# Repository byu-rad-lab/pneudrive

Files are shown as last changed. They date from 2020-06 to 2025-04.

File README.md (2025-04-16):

# PneuDrive Pressure Control System

This repository contains all of the designs, code, and instructions needed to create a low level pressure controller designed for pneumatically actuated robots. This pressure controller is designed to use relatively inexpensive off-the-shelf components and to favor simplicity in an effort to make it easy to understand and adapt for different applications.

Here is a [video](https://bit.ly/3QkrEqO) that is a brief overview of the system.

<!-- add picture of boards from resources folder -->
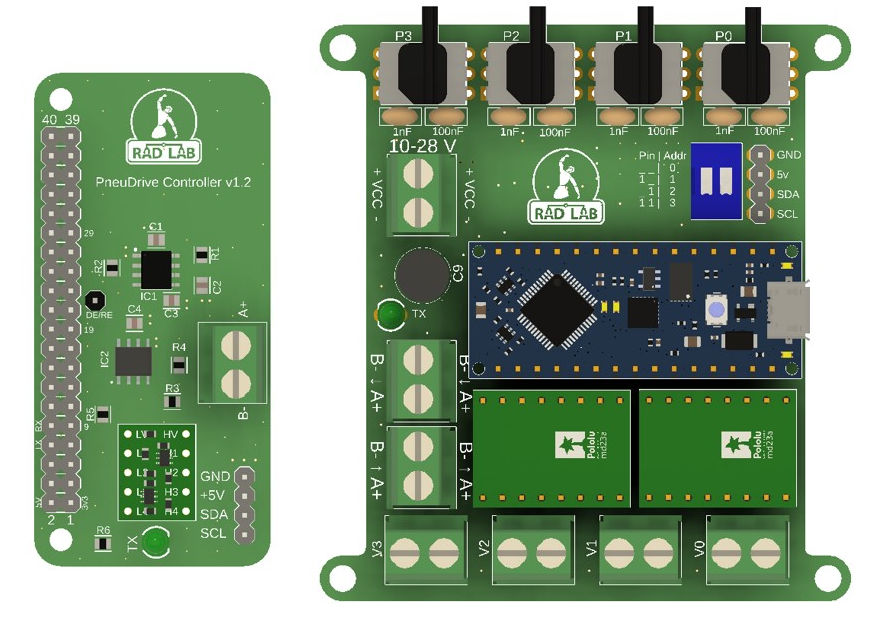
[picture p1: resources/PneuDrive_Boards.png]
PneuDrive boards


The pressure control system consists of one single-board-computer (SBC) acting as the ROS master and communicating serially with one or more Arduinos. The SBC needs to be capable of running ROS/Ubuntu (e.g. Raspberry Pi, NVIDIA Jetson, Odroid). We use the [ODROID N2+](https://www.hardkernel.com/shop/odroid-n2-with-4gbyte-ram-2/). We also provide python bindings that allow you to interact with the pressure controller without ROS.

Each Arduino performs high-rate (~1 kHz) pressure control of up to 4 chambers and transmits pressure data back to the ROS master. A high level diagram of the pressure control system can be seen in the figure below:

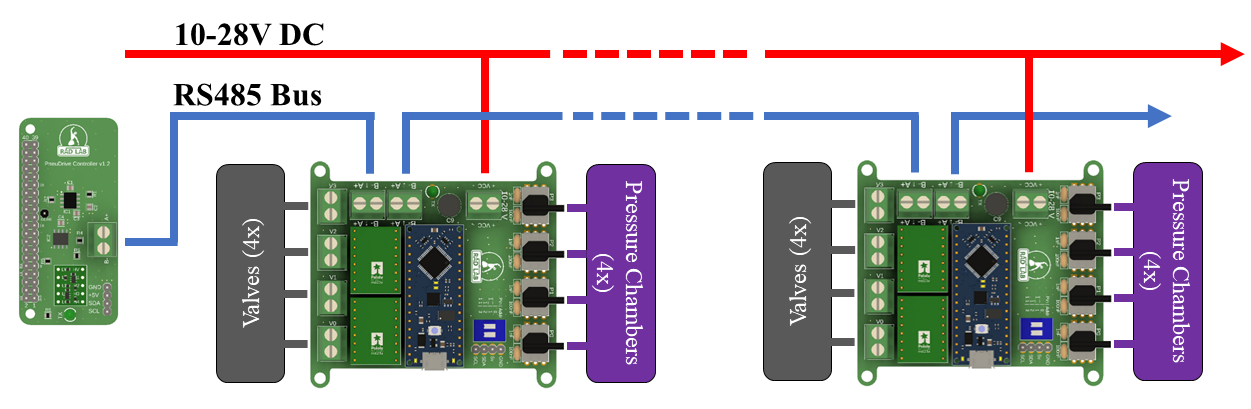
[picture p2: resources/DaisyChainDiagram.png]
PneuDrive system


## Dependencies

## Installation
If the SBC is connected to the internet, the easiest way to use PneuDrive is to clone the repository directly onto the SBC. If the SBC is not connected to the internet, you can clone the repository onto another computer and then copy it over to the SBC using a tool like scp over a local network:

``` console
scp -r <path to pneudrive on computer> <username@SBC_IP_ADDRESS>:<path to desired location on SBC>
```

If you intend to use PneuDrive with ROS, just make sure the package is placed into the src directory of a ROS workspace. Once the pneudrive package in in the src directory, you can build it using ```colcon build``` from the root of the workspace.

If you intend to use PneuDrive without ROS (i.e. using the python bindings), you can place the package anywhere on the SBC. Python bindings are implemented using pybind11, so when cloning the repository, it is important to pass ```--recurse-submodules``` to git to ensure that pybind11 is cloned as well:

``` console
git clone --recurse-submodules <git url>
```

To build the bindings, you will just need to navigate to the python_bindings directory and build the bindings manually with cmake:

``` console
cd python_bindings
mkdir build
cd build
cmake ..
make
```

## How is it organized

This repository is structured as a ROS package. It is designed to be placed in a ROS workspace on the SBC used for pressure control. There are however several other directories not necessary for a ROS package:

* **pcb_design** - this directory contains all of the wiring diagrams and PCB schematics. Instructions for the population of the PCB as well as wiring the entire pressure controller are found here.
* **odroid_setup** - this directory contains all of instructions and files necessary to set up an ODROID for use as the ROS master in a pressure control system.
* **arduino_firmware** - this directory contains the instructions and code needed to program the arduinos to act as high rate pressure controllers.
* **python_bindings** - this directory contains python bindings to interact with PneuDrive independent of ROS, in a python scripting environment.

## Steps to create a pressure control system

1. Use the instructions and schematics in the **pcb_design** directory to order and assemble the necessary components to construct a PneuDrive controller PCB and several embedded PCBs.
2. Use the instructions and files in the **odroid_setup** directory to setup the SBC as the ROS master
3. Use the instructions and files in the **arduino_firmware** directory to program each arduino as a high-rate pressure controller

## Running the PneuDrive ROS Node

Once the SBC boots up it you can ssh into it with ```ssh ubuntu@192.168.0.xxx```. The username is ```ubuntu``` and the password is ```temppwd```. This process might be slightly different depending on your SBC.

Once you are logged in, you can launch the pressure control ROS node (along with a roscore) using the following command:

``` shell
ros2 launch pneudrive rs485_pressure.launch.py numjoints:=[number of joints]
```

where the ```numjoints``` command line argument is required and tells the node how many joints to look for on the serial bus. 

This creates a ROS node called "PressureController". Depending on ```numjoints```, the node will create addresses for each joint. The node then creates publishers and subscribers for every joint specified by the addresses. If the SBC cannot find all of the specified addresses, the node throw an error and shut down. If this happens, here are some common fixes:

* Make sure your wires are all connected securely and correctly.
* Make sure that each pressure control board dip switch is set to the proper address. The dip switch positions are printed on the pcb and they should match what is specified in the yaml file. For example, if I have a 3 joint arm, I would make sure that the first joint is set to 0 then the next as 1 and the last as 2, with those same addresses specified in the code. 
* Make sure you didn't flip the A+ and B- wires when wiring up the connectors. We chose to use screw terminals for ease of use, but this does make flipping wires easier if you aren't being careful. 

When the node launches, it will print out all of the joints it detected and start the node.

## Citation

If you use PneuDrive in your research, please cite the our paper:

```bibtex

 @inproceedings{
	 Johnson_Cheney_Cordon_Killpack_2024, 
	 address={San Diego, CA, USA}, 
	 title={PneuDrive: An Embedded Pressure Control System and Modeling Toolkit for Large-Scale Soft Robots}, 
	 rights={https://doi.org/10.15223/policy-029}, 
	 ISBN={9798350381818}, 
	 url={https://ieeexplore.ieee.org/document/10521958/}, 
	 DOI={10.1109/RoboSoft60065.2024.10521958}, 
	 booktitle={2024 IEEE 7th International Conference on Soft Robotics (RoboSoft)}, 
	 publisher={IEEE}, 
	 author={Johnson, Curtis C. and Cheney, Daniel G. and Cordon, Dallin L. and Killpack, Marc D.}, 
	 year={2024}, 
	 month=apr, 
	 pages={786–792}, 
	 language={en} 
 }

```

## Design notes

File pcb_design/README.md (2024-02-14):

This directory contains everything you need to order and assemble the PCBs needed for PneuDrive. 

# PnueDrive Controller Board
### Design Files
1. All design files (Bill of Materials, 3d step file, .sch, .brd, and a pdf of the schematic) are located in PnueDrive-Controllerv1.2-Designs.zip.

### Ordering PCB
1. Any PCB manufacturer can be used, but we have used JLCPCB in the past. Go to their [website](https://jlcpcb.com/), click upload gerber file, and upload pneudrive_controllerv1.2_gerbers.zip. After processing, it should say "Detected 4 layer board of 65x31mm(2.56x1.22 inches) ."
2. Every manufacturing option can remain default except for the following: **Remove Order Number: Specify a Location**
3. If you want, you can order a stencil to make soldering the SMT components easier. We have not done this since there are only 1 or 2 controller boards that need to be assembled.

### Ordering Components
1. The Bill of Materials (BoM) PneuDrive BoM - Controllerv1.2.pdf. The BoM contains links to purchase components, descriptions, and part numbers. The total price as of 2023 is $5.87 USD.
2. You will also need female headers to plug things into and the logic level shifter from pololu.

### Assembly
1. Solder the SMT components to the board before any of the through hole components. This is because the through hole components will get in the way of the hot air rework station. [Here](https://www.youtube.com/watch?v=fYInlAmPnGo&pp=ygUWc210IHNvbGRlcmluZyB0dXRvcmlhbA%3D%3D) is a good tutorial on how to do SMT soldering.

# PneuDrive Embedded Board
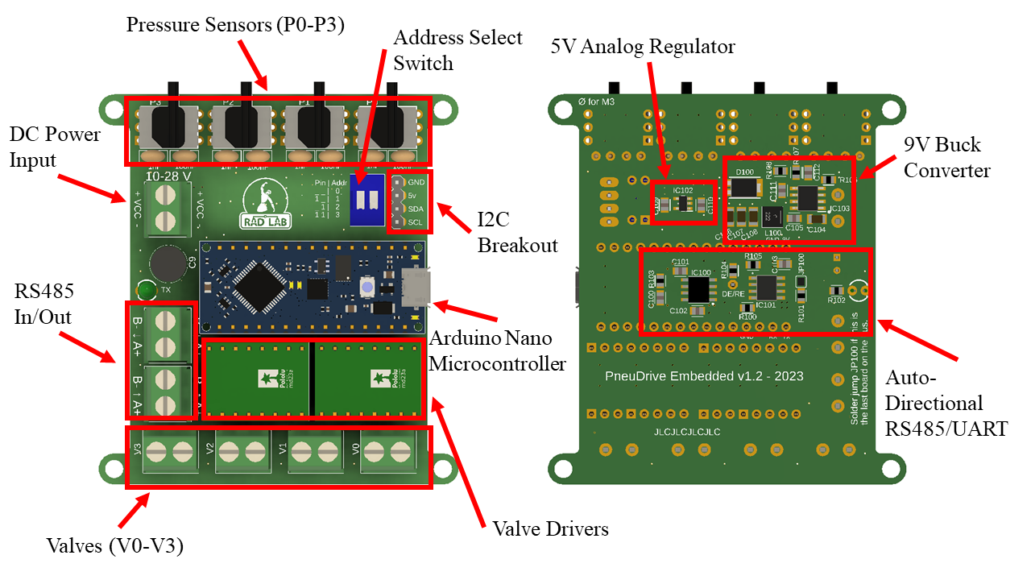
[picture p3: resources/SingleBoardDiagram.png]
Embedded Board


### Design Files
1. All design files (Bill of Materials, 3d step file, .sch, .brd, and a pdf of the schematic) are located in PneuDrive-Embeddedv1.2-Designs.zip.

### Ordering PCB
1.  Go to their [website](https://jlcpcb.com/), click upload gerber file, and upload pneudrive_embeddedv1.2_gerbers.zip After processing, it should say "Detected 4 layer board of 75x69mm(2.95x2.72 inches)."
2.  Every option can remain default except for the following: **Remove Order Number: Specify a Location**
3.  Order Stencil together with PCB. This costs extra, but since the embedded boards typically are assembled in volume, it is worth it.
4.  All the stencil options can stay default except the following: **Stencil Side: Bottom**

### Ordering Components
1. The Bill of Materials (BoM) PneuDrive BoM - Embeddedv1.2.pdf. The BoM contains links to purchase components, descriptions, and part numbers. The total price as of 2023 is $156.74 USD.
2. You will also need female headers to plug things into and the a4990 motor driver breakouts from pololu.

### Assembly
1. Solder the SMT components on the bottom before any of the through hole components. This is because the through hole components will get in the way of the hot air rework station. [Here](https://www.youtube.com/watch?v=fYInlAmPnGo&pp=ygUWc210IHNvbGRlcmluZyB0dXRvcmlhbA%3D%3D) is a good tutorial on how to do SMT soldering.

# Consumables

For assembly, we used the following:
*  [Solder Paste](https://www.amazon.com/Wonderway-Soldering-Electronics-CELLPHONE-Repairing/dp/B0BLSJQPR6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) ~$15 USD
*  [Flux](https://www.amazon.com/Smooth-Flow-No-Clean-syringe-plunger/dp/B08KJRCYRH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) ~$15 USD
*  [Solder Wire](https://www.amazon.com/Dia0-032in-0-11lb-Precision-Electronics-Soldering/dp/B07Q167J98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) ~$10 USD

# Tools
You'll need
* A soldering iron
* A hot air rework station (for SMT components)

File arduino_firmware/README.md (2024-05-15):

# PneuDrive Firmware

## Introduction
This Arduino code is designed for controlling valves using the A4990 motor driver and interfacing with pressure sensors. It provides functionality for reading pressure data and adjusting valve positions accordingly. The code and hardware is designed for each module to be a node on an RS485 bus for high speed and robust communication.

## Valve Command Signals
Valve PWM commands are on the interval [-400, 400]. 
- -400 corresponds to commanding -1 amp (vent), and 400 corresponds to +1 amp (fill).
- The driver boards actively limit current to 0.7 amps, so any command above 0.7 amps will result in 0.7 amps on the hardware.

## Timer Frequencies
- The code makes use of timers for PWM control. It changes the timer frequencies to eliminate annoying hum when controlling the valves.
- Note that changing timer frequencies may affect the built-in delay() and millis() functions.

## Dependencies
- This code relies on the `A4990ValveInterface` library.

## Installation
1. Ensure you have the necessary hardware set up (i.e. the PCBs are all built)
2. We use the [PlatformIO extension](https://marketplace.visualstudio.com/items?itemName=platformio.platformio-ide), so the configuration files are already included. If you are using the Arduino IDE, you will need to manually install the libraries and configure the project. 
3. Open this directory with Platform IO
4. Install the required Arduino libraries (if using Arduino IDE), or let PlatformIO do that for you based on the platform.ini
5. Upload main.cpp to your Arduino Nano Every from PlatformIO. 

## Usage
1. Connect the pressure sensors as specified in the code.
2. Adjust the parameters like `MAX_INPUT`, `saturation_error`, and `kp` to suit your application.
3. Monitor valve commands and pressure data through the Serial monitor if `DEBUG_MODE` is enabled.
4. Use the code to control valves and read pressure data as needed.

## Functions and Their Descriptions

### `byteToShorts(unsigned short *short_array, const byte *byte_array)`
- Converts an array of 8 bytes to an array of 4 shorts.
- Used to decode incoming data.

### `shortToBytes(const unsigned short *short_array, byte *byte_array)`
- Converts an array of 5 shorts to an array of 10 bytes in big-endian format.
- Used to prepare outgoing data.

### `handleIncomingBytes()`
- Handles incoming data from the Serial port.
- Checks for device addresses and processes pressure commands.
- Responds with pressure data if the device address matches.

### `readPressureData()`
- Reads pressure data from analog pins and stores it for use in control.

### `custom_delay(int seconds)`
- Custom delay function for waiting a specified number of seconds since we can't use the built-in delay() function with the modified timer frequencies.

### `getrs485address()`
- Retrieves the RS485 address based on the state of DIP switches.

### `speedupPWM()`
- Configures timer frequencies to eliminate audible noise from valve control.

### `setup()`
- Initializes the hardware and serial communication.
- Sets up timer frequencies and other parameters.

### `loop()`
- The main loop of the program.
- Reads pressure data, processes it, and adjusts valve commands accordingly.

## Author
- Curtis Johnson

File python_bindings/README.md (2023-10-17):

To build the bindings, you will just need to navigate to the python_bindings directory and build the bindings manually with cmake:

``` console
cd python_bindings
mkdir build
cd build
cmake ..
make
```

Once they are built, an importable python module called pneudrive_py will show up as a shared library in the build directory. You can import this module into any python script and use it to communicate with the pressure controllers. Here is a simple example:

``` python
import numpy as np
from pneudrive_py import PressureController

uart_port = '/dev/ttyS1'
num_devices = 4
my_controller = PressureController(uart_port, num_devices)

#check communication with all expected devices
my_controller.ping_devices()

pressure_cmd = np.array([1,2,3,4])
for i in range(num_devices):
    my_controller.set_pressure_commands(i, pressure_cmd)
    data = my_controller.get_pressure_data(i)

```

Setting the pressure commands for the ith device using ``` set_pressure_commands()``` initiates a call and repsonse transmission. The SBC controller will send the commands to the embedded device and the embedded device will respond with pressure measurements, accessible in Python via ``` get_pressure_data()```. 

Note that this means that successive calls to ```get_pressure_data()``` for the same device will return the same data. If you want to get new data, you will need to call ```set_pressure_commands()``` again.

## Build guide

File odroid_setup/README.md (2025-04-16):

## Setting Up an Odroid with Ubuntu for Pneumatic Drive Control

### Requirements

- [Download Balena Etcher](https://etcher.balena.io/#download-etcher)
- Ubuntu image: Find the image in JDrive at `groups/rad-software/odroid_pneudrive_22_04.zip`

### Flashing Ubuntu Image to SD Card

1. Open Balena Etcher.
2. Select the downloaded Ubuntu image.
3. Insert a 16 GB SD card.
4. Flash the image to the SD card.

### Setting Up Odroid

#### Connect Hardware

- Insert the flashed SD card into the Odroid.
- Connect the Odroid to power and Ansible.

#### SSH into Odroid

- SSH into the Odroid: `ssh ubuntu@192.168.0.200`
  - Password: `temppwd`

#### Ensure Correct File Structure

Ensure the directory contains the Pneudrive package. Ensure that it is the most up-to-date version.

#### Change Static IP Address

1. Check the [Lab Wiki](https://github.com/byu-rad-lab/rad-lab-wiki/blob/main/infrastructure/lab_ip_addresses.md) for an available IP address.
2. Update the Lab Wiki with your IP address and device information.
3. Print a label and attach it to the Odroid for future reference.
4. Determine the network interface with `ip addr` (likely `eth0`).
5. Edit the Netplan configuration file (Change ONLY the IP address): ```sudo nano /etc/netplan/radlabconfig.yaml ```
6. Go edit the .bashrc file so that ROS_IP is the ip address you just changed to.
7. Apply the changes: ```sudo netplan apply```
8. Reconnect to the Odroid with the new IP address.
9. Reboot and check the updated IP address:

```
sudo shutdown now -r
ssh ubuntu@<new_ip_address>
ip addr show
```

9. Confirm that the IP address has been updated successfully using `ip addr`.

### Getting Pneudrive to Run

1. Navigate to the `ros_ws` directory and delete the `devel` and `build` directories using the command `rm -rf devel build`.
2. Navigate to the home directory and source the `.bashrc` file by running the command `source .bashrc`.
3. Navigate back to the `ros_ws` directory and run the command `colcon build`.
4. Once the `colcon build` is complete, verify that the Pneudrive package can be found by running the command `ros2 pkg list`.
- You should see a list of packages including pneudrive.
- If pneudrive is not present in the list of packages, keep trying variations of what is listed above until it works.

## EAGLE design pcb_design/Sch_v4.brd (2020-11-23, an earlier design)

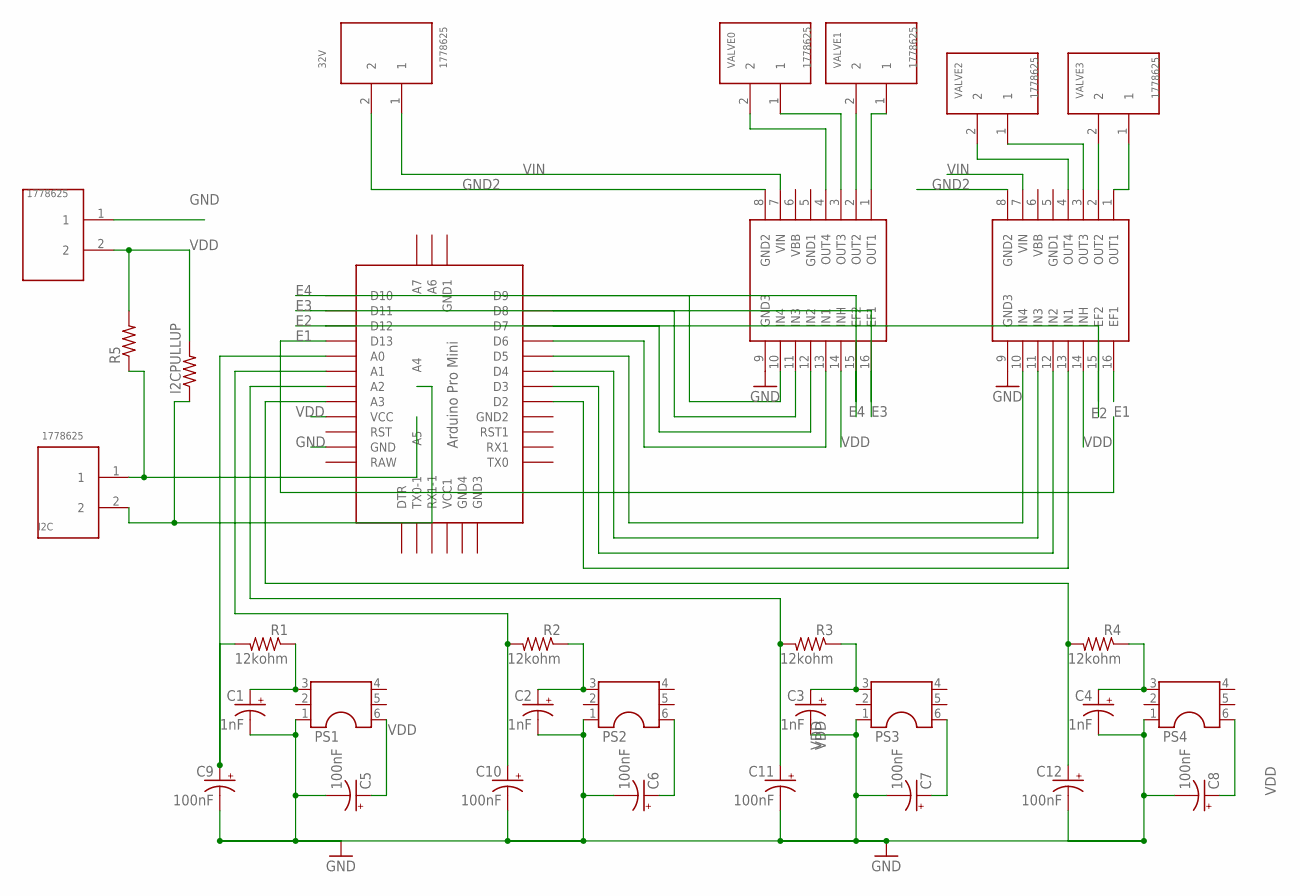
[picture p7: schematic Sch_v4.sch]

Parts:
5V, 32V: 1778625
C1, C2, C3, C4: 1nF; E2,5-5
C5, C6, C7, C8, C9, C10, C11, C12: 100nF; E2,5-5
I2C: 1778625
I2CPULLUP: R-US_0204/7; 0204/7
PS1, PS2, PS3, PS4: ABPDRNN100PGAA5
R1, R2, R3, R4: 12kohm; 0204/7
R5: R-US_0204/7; 0204/7
U$1: ABK-PRO-MINI
U$2, U$3: A4990
VALVE0, VALVE1, VALVE2, VALVE3: 1778625

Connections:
E1: U$1.D13, U$3.16 (EF1)
E2: U$1.D12, U$3.15 (EF2)
E3: U$1.D11, U$2.16 (EF1)
E4: U$1.D10, U$2.15 (EF2)
GND: 5V.1, C1.-, C2.-, C3.-, C4.-, C5.-, C6.-, C7.-, C8.-, C9.-, C10.-, C11.-, C12.-, PS1.1, PS2.1, PS3.1, PS4.1, U$1.GND, U$2.9 (GND3), U$3.9 (GND3)
GND2: 32V.2, U$2.8 (GND2), U$3.8 (GND2)
unnamed: C1.+, PS1.3, R1.1
unnamed: C2.+, PS2.3, R2.1
unnamed: C3.+, PS3.3, R3.1
unnamed: C4.+, PS4.3, R4.1
unnamed: U$2.2 (OUT2), VALVE1.2
unnamed: U$2.1 (OUT1), VALVE1.1
unnamed: U$2.3 (OUT3), VALVE0.1
unnamed: U$2.4 (OUT4), VALVE0.2
unnamed: C9.+, R1.2, U$1.A0
unnamed: C10.+, R2.2, U$1.A1
unnamed: C11.+, R3.2, U$1.A2
unnamed: C12.+, R4.2, U$1.A3
unnamed: U$3.1 (OUT1), VALVE3.1
unnamed: U$3.2 (OUT2), VALVE3.2
unnamed: U$3.3 (OUT3), VALVE2.1
unnamed: U$3.4 (OUT4), VALVE2.2
unnamed: U$1.D2, U$3.13 (IN1)
unnamed: U$1.D3, U$3.12 (IN2)
unnamed: U$1.D4, U$3.11 (IN3)
unnamed: U$1.D5, U$3.10 (IN4)
unnamed: I2C.1, R5.1, U$1.A5
unnamed: U$1.D6, U$2.13 (IN1)
unnamed: U$1.D7, U$2.12 (IN2)
unnamed: U$1.D8, U$2.11 (IN3)
unnamed: U$1.D9, U$2.10 (IN4)
VDD: 5V.2, C5.+, C6.+, C7.+, C8.+, I2C.2, I2CPULLUP.1, I2CPULLUP.2, PS1.6, PS2.6, PS3.6, PS4.6, R5.2, U$1.A4, U$1.VCC, U$2.14 (INH), U$3.14 (INH)
VIN: 32V.1, U$2.7 (VIN), U$3.7 (VIN)

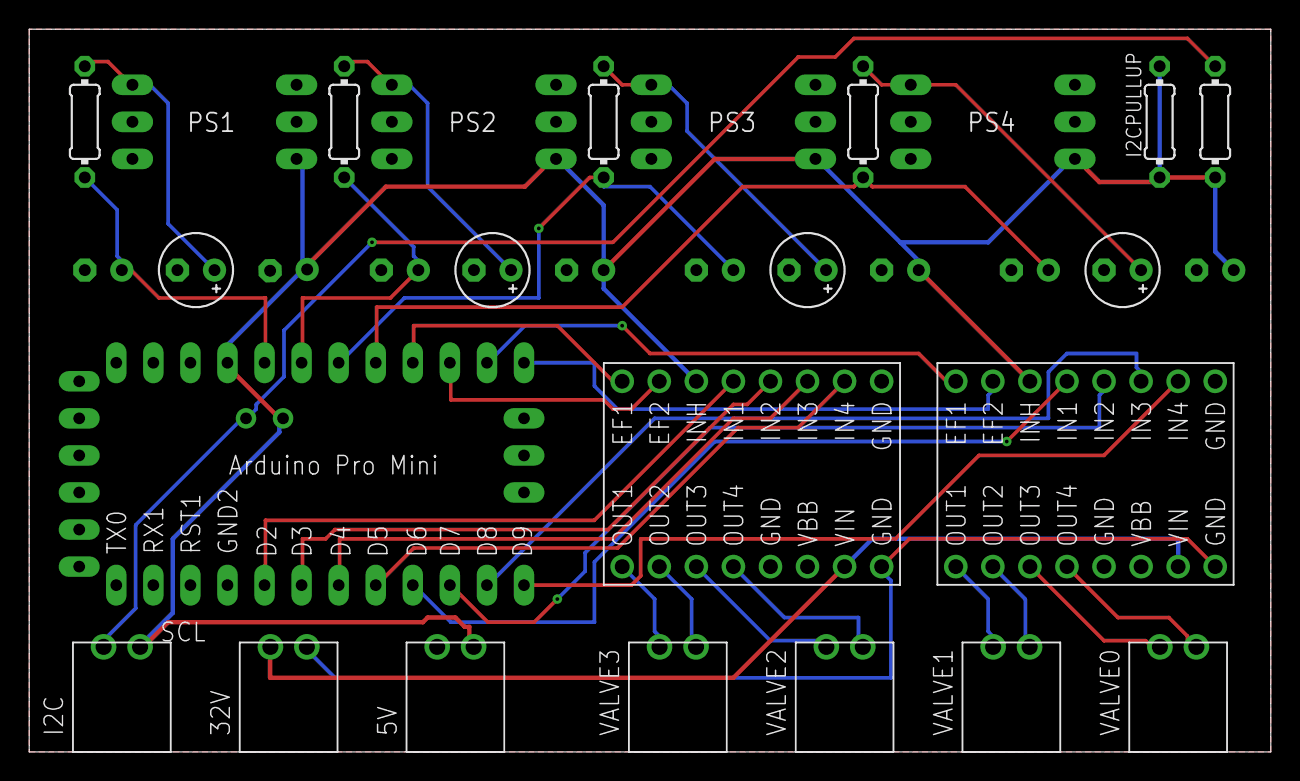
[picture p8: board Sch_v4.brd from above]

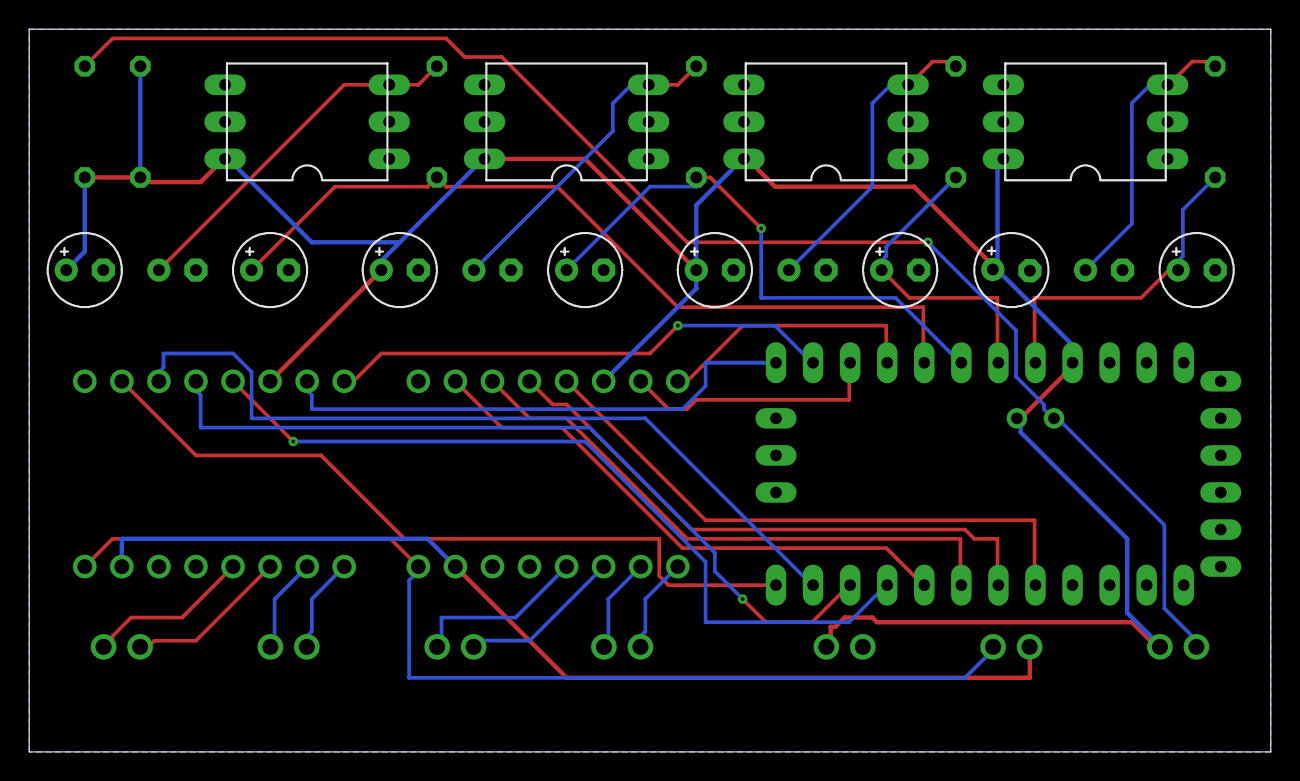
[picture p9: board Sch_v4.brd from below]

Board: 2 copper layers, 85.1 x 49.5 mm, 32 parts (12 on the bottom side), 33 nets.

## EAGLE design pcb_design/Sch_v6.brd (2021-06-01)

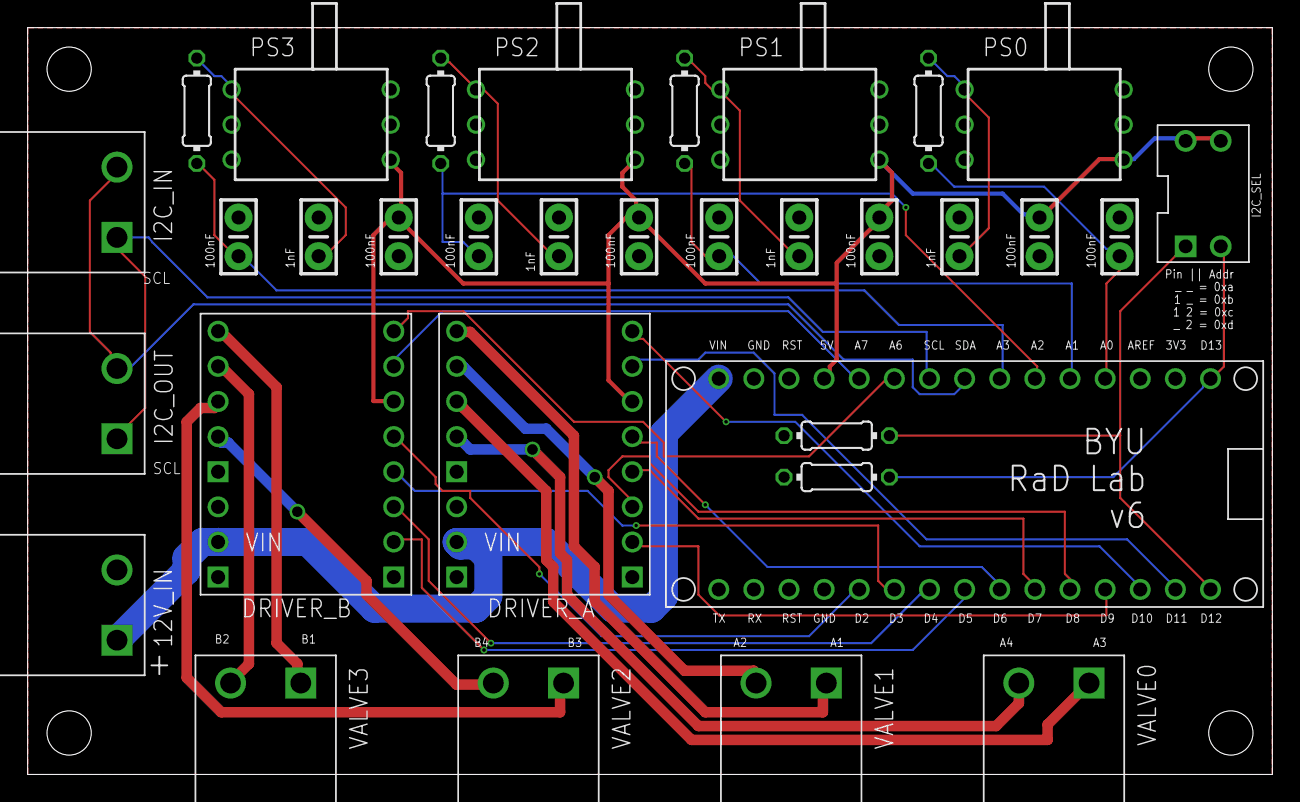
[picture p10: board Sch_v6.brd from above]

Board: 2 copper layers, 90.0 x 54.0 mm, 33 parts (0 on the bottom side), 36 nets.

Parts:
12V_IN: PHOENIX_CONTACT_1759017
C1, C2, C3, C4: 1nF; CERAMIC_CAPACITOR
C5, C6, C7, C8, C9, C10, C11, C12: 100nF; CERAMIC_CAPACITOR
DRIVER_A: A4990_DUAL_MOTOR_DRIVER_CARRIER
DRIVER_B: A4990_DUAL_MOTOR_DRIVER_CARRIER
I2C_IN, I2C_OUT: PHOENIX_CONTACT_1759017
I2C_SEL: 2PIN_DIP_DS01-254-S-02BE
NANO1: ARDUINO_NANO_EVERY
PS0, PS1, PS2, PS3: PRESSURE_SENSOR_ABPDRNN100PGAA5
R1, R2, R3, R4: 12k; 0204/7
R5, R6: 4.7k; 0204/7
VALVE0, VALVE1, VALVE2, VALVE3: PHOENIX_CONTACT_1759017

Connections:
5V: C5.2, C6.2, C7.2, C8.2, DRIVER_A.14, DRIVER_B.14, I2C_SEL.1B, I2C_SEL.2B, NANO1.12, PS0.6, PS1.6, PS2.6, PS3.6
12V: 12V_IN.1, DRIVER_A.7, DRIVER_B.7, NANO1.15
A0: C9.1, NANO1.4, R1.2
A1: C10.1, NANO1.5, R2.2
A2: C11.1, NANO1.6, R3.2
A3: C12.1, NANO1.7, R4.2
D2: DRIVER_B.13, NANO1.20
D3: DRIVER_B.12, NANO1.21
D4: DRIVER_B.11, NANO1.22
D5: DRIVER_B.10, NANO1.23
D6: DRIVER_A.13, NANO1.24
D7: DRIVER_A.12, NANO1.25
D8: DRIVER_A.11, NANO1.26
D9: DRIVER_A.10, NANO1.27
EF1_A: DRIVER_A.16, NANO1.28
EF1_B: DRIVER_B.16, NANO1.10
EF2_A: DRIVER_A.15, NANO1.29
EF2_B: DRIVER_B.15, NANO1.11
GND: C1.2, C2.2, C3.2, C4.2, C5.1, C6.1, C7.1, C8.1, C9.2, C10.2, C11.2, C12.2, DRIVER_A.5, DRIVER_A.9, DRIVER_B.5, DRIVER_B.9, NANO1.14, NANO1.19, PS0.1, PS1.1, PS2.1, PS3.1, R5.2, R6.1
MOTOR_GND: 12V_IN.2, DRIVER_A.8, DRIVER_B.8
unnamed: C1.1, PS0.3, R1.1
unnamed: C2.1, PS1.3, R2.1
unnamed: C3.1, PS2.3, R3.1
unnamed: C4.1, PS3.3, R4.1
unnamed: DRIVER_A.2, VALVE1.2
unnamed: DRIVER_A.1, VALVE1.1
unnamed: DRIVER_A.3, VALVE0.1
unnamed: DRIVER_A.4, VALVE0.2
unnamed: DRIVER_B.1, VALVE3.1
unnamed: DRIVER_B.2, VALVE3.2
unnamed: DRIVER_B.3, VALVE2.1
unnamed: DRIVER_B.4, VALVE2.2
unnamed: I2C_SEL.1A, NANO1.30, R6.2
unnamed: I2C_SEL.2A, NANO1.1, R5.1
SCL: I2C_IN.1, I2C_OUT.1, NANO1.9
SDA: I2C_IN.2, I2C_OUT.2, NANO1.8

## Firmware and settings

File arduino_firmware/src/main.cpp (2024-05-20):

#include "A4990ValveInterface.h"

/*
  NOTE ON VALVE COMMAND SIGNALS
  -----------------------------
  Valve PWM commands are on the interval [-400,400].

  -400 corresponds to commanding -1 amp (vent) and 400 corresponds to +1 amp (fill).
  The driver boards actively limit current to 0.7 amps however,
  so any command above 0.7 amps will result in 0.7 amps on the hardware. See current2PWM() function below.

  Negative numbers mean vent and positive mean fill.
  If the valve is flipped, the wires need to be switched.

*/

/*
  IMPORTANT NOTE ON TIMER FREQUENCIES
  ------------------------------------
  On the Arduino Nano Every (ATmega 4809 chipset), there are two timers related to the PWM pins we
  using: TCA for D5 and D9 and TCB for D3 and D6.

  The default pwm freq for these pins is 975 Hz = fclk_per/64 (where fclk_per is the peripheral clock,
  and is set to 62.4kHz by default. This freq causes a really annoying hum when the valves are being
  controlled. To get rid of this, we prescale the timers to 31.2kHz = fclk_per/2 in speedupPWM() because
  31.2 kHz is well outside the range of what a human can hear.

  TCB can be changed like this without causing any issues. TCA, on the other hand, is used by the
  built-in delay() and millis() functions. Since we changed the freq by a factor of 32 (PRESCALER),
  this means that millis() now reports 32 times the actual time passed (e.g. millis()/PRESCALER is the
  actual number of milliseconds that have passed).

  Another consequence of changing TCA is that delay() now (for some reason) can only delay up to
  32,768 (2^16/2) which corresponds to an actual delay of 32768/32 = 1024 ms. So, there is a custom
  delay function defined custom_delay() which allows you to delay for longer than 1024 ms. Since
  delay() function isn't used in the control loop, this is adequate for our needs.
*/

A4990ValveInterface valves;

short valve_cmd[4] = { 0, 0, 0, 0 };
short VENT_CMD[4] = { -400, -400, -400, -400 };
short FILL_CMD[4] = { 400, 400, 400, 400 };

const unsigned short MAX_INPUT = 400;
unsigned short saturation_error = 40;
unsigned short kp = MAX_INPUT / saturation_error;
unsigned short kd = 20;

#define PRESCALER 32
#define ONE_SECOND 32000
#define BYTES_IN_PACKET 10
#define DEBUG_MODE false

byte outgoingBytes[BYTES_IN_PACKET] = { 0, 0, 0, 0, 0, 0, 0, 0, 0, 0 };
byte incomingDataBytes[BYTES_IN_PACKET - 2] = { 0, 0, 0, 0, 0, 0, 0, 0 };

unsigned short outgoingShorts[BYTES_IN_PACKET / 2] = { 0, 0, 0, 0, 0 };

unsigned short rs485_address = 0x0000;
unsigned short pressure_commands[4] = { 102, 102, 102, 102 }; // ADC value of 102 corresponds to 0 kPa
unsigned short incoming_commands[4] = { 102, 102, 102, 102 };
unsigned short pressure_data[4] = { 102, 102, 102, 102 };
unsigned short prev_pressure_data[4] = { 102, 102, 102, 102 };
unsigned long alpha = 210;

// Function to convert array of 8 bytes to array of 4 shorts
void byteToShorts(unsigned short* short_array, const byte* byte_array)
{
  unsigned int byteLength = 8;
  for (size_t i = 0; i < byteLength; i += 2)
  {
    int byteIndex = i;
    short_array[i / 2] = ((short)byte_array[byteIndex] << 8) | byte_array[byteIndex + 1];
  }

  if (DEBUG_MODE)
  {
    Serial.print("Incoming shorts: ");
    for (int i = 0; i < 4; i++)
    {
      Serial.print(short_array[i], DEC);
      Serial.print(" ");
    }
    Serial.println();
  }
}

void saveIfValid(unsigned short* incoming_commands, unsigned short* pressure_commands)
{
  //if any of the incoming commands are out of bounds, don't save the entire array since it got corrupted

  for (int i = 0; i < 4; i++)
  {
    if (incoming_commands[i] < 0 || incoming_commands[i] > 1023)
    {
      return;
    }
  }

  // all commands are valid, save them
  for (int i = 0; i < 4; i++)
  {
    pressure_commands[i] = incoming_commands[i];
  }
}

// Function to convert array of 5 shorts to array of 10 bytes, but in big endian
void shortToBytes(const unsigned short* short_array, byte* byte_array)
{
  int shortLength = 5;
  for (size_t i = 0; i < shortLength; i++)
  {
    int byteIndex = i * 2;
    unsigned char* bytePtr = (unsigned char*)&short_array[i];

    // Convert from little endian to big endian
    byte_array[byteIndex] = bytePtr[1];     // LSB
    byte_array[byteIndex + 1] = bytePtr[0]; // MSB
  }

  if (DEBUG_MODE)
  {
    Serial.print("Outgoing bytes: ");
    for (int i = 0; i < 10; i++)
    {
      Serial.print(byte_array[i], DEC);
      Serial.print(" ");
    }
    Serial.println();
  }
}

void handleIncomingBytes()
{
  byte firstByte = 0;
  while (Serial1.available() > 0)
  {
    if (DEBUG_MODE)
    {
      Serial.print("Available bytes: ");
      Serial.println(Serial1.available(), DEC);
    }
    byte secondByte = Serial1.read();

    if (DEBUG_MODE)
    {
      Serial.print("First byte: ");
      Serial.println(firstByte, DEC);
      Serial.print("Second byte: ");
      Serial.println(secondByte, DEC);
    }

    unsigned short short1 = (firstByte << 8) | secondByte;

    if (short1 == rs485_address)
    {
      if (DEBUG_MODE)
      {
        Serial.println("Address found!");
      }

      size_t numBytesRead = Serial1.readBytes(incomingDataBytes, BYTES_IN_PACKET - 2);

      if (DEBUG_MODE)
      {
        Serial.print("Incoming bytes: ");
        for (int i = 0; i < 8; i++)
        {
          Serial.print(incomingDataBytes[i], DEC);
          Serial.print(" ");
        }
        Serial.println();
      }

      if (numBytesRead == 8)
      {
        Serial1.flush();
        if (Serial1.availableForWrite() == SERIAL_TX_BUFFER_SIZE - 1)
        {
          size_t numBytesWritten = Serial1.write(outgoingBytes, BYTES_IN_PACKET);
          if (DEBUG_MODE)
          {
            Serial.print("Outgoing bytes written: ");
            Serial.println(numBytesWritten, DEC);
          }
        }
        byteToShorts(incoming_commands, incomingDataBytes);
        saveIfValid(incoming_commands, pressure_commands);

        firstByte = 0;
      }
      else
      {
        // Serial.print("Timeout. Bytes read: ");
        // Serial.println(numBytesRead, DEC);
      }
    }
    else
    {
      if (DEBUG_MODE)
      {
        Serial.println("Address not found.");
      }

      firstByte = secondByte;
    }
  }
}

void readPressureData()
{
  for (int i = 0; i < 4; i++)
  {
    //update delayed vars before reading new data
    prev_pressure_data[i] = pressure_data[i];

    // low pass filter with fixed point math for speed
    unsigned long temp = alpha * pressure_data[i] + (256 - alpha) * analogRead(A0 + i); // max value is 1023*256 = 261888, need a long to prevent overflow
    pressure_data[i] = static_cast<unsigned short>(temp / 256);                         // divide by 256, back to short range
    outgoingShorts[i + 1] = pressure_data[i];
  }

  if (DEBUG_MODE)
  {
    Serial.print("Pressure data: ");
    for (int i = 0; i < 4; i++)
    {
      Serial.print(pressure_data[i], DEC);
      Serial.print(" ");
    }
    Serial.println();
  }
}

void custom_delay(int seconds)
{
  for (int s = 0; s < seconds; s++)
  {
    delay(ONE_SECOND);
  }
}

int getrs485address()
{
  unsigned short rs485addr;
  int one;
  int two;

  pinMode(10, INPUT_PULLUP);
  pinMode(11, INPUT_PULLUP);

  one = digitalRead(10);
  two = digitalRead(11);

  if (one == HIGH && two == HIGH)
  {
    rs485addr = 0xFFFF - 0;
  }
  else if (one == LOW && two == HIGH)
  {
    rs485addr = 0xFFFF - 1;
  }
  else if (one == HIGH && two == LOW)
  {
    rs485addr = 0xFFFF - 2;
  }
  else if (one == LOW && two == LOW)
  {
    rs485addr = 0xFFFF - 3;
  }
  return rs485addr;
}

void speedupPWM()
{
  /* see section 20.5.1 of http://ww1.microchip.com/downloads/en/DeviceDoc/ATmega4808-4809-Data-Sheet-DS40002173A.pdf
    for this register settings. Note that by default, fclk_per = 62.4 kHz.
    Humans can hear 20 Hz to 20 kHz, so a 31.2kHz freq should be out of hearing range.
    Also see section 5.4.1 for syntax used here.
    | is "bitwise or" commonly used to set multiple bits at once in a register.
    TCA_SINGLE_CLKSEL_DIV2_gc | TCA_SINGLE_ENABLE_bm --> 0,0,1,0 OR 0,0,0,1 = 0,0,1,1

    READ TIMER FREQUENCY NOTE AT TOP
*/
  cli(); // Disable Interrupts

  // Set timer frequencies to 31.2 kHz
  TCB0.CTRLA = (TCB_CLKSEL_CLKDIV2_gc) | (TCB_ENABLE_bm);
  TCA0.SINGLE.CTRLA = TCA_SINGLE_CLKSEL_DIV2_gc | TCA_SINGLE_ENABLE_bm;

  sei(); // Enable Interrupts
}

void setup()
{
  pinMode(LED_BUILTIN, OUTPUT);
  pinMode(A0, INPUT);
  pinMode(A1, INPUT);
  pinMode(A2, INPUT);
  pinMode(A3, INPUT);

  speedupPWM();
  analogReference(EXTERNAL);

  rs485_address = getrs485address();

  if (DEBUG_MODE)
  {
    Serial.begin(115200);
    Serial.print("Device address: ");
    Serial.println(rs485_address, DEC);
  }

  Serial1.begin(1000000); // RS485 Serial port
  Serial1.setTimeout(1);

  outgoingShorts[0] = rs485_address;

  valves.setSpeeds(VENT_CMD);

  custom_delay(2);
}

void loop()
{
  readPressureData();
  shortToBytes(outgoingShorts, outgoingBytes);
  handleIncomingBytes();

  for (int i = 0; i < 4; i++)
  {
    int proportional = kp * (pressure_commands[i] - pressure_data[i]);
    int derivative = kd * (pressure_data[i] - prev_pressure_data[i]);
    valve_cmd[i] = proportional - derivative;
  }

  valves.setSpeeds(valve_cmd);

  if (DEBUG_MODE)
  {
    Serial.print("Valve commands: ");
    for (int i = 0; i < 4; i++)
    {
      Serial.print(valve_cmd[i], DEC);
      Serial.print(" ");
    }
    Serial.println();
  }
}

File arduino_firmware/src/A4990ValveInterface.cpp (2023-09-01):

/*
   This code is a modified version of a library that Pololu released for the A4990 Motor Driver.
   This library can be found here: https://github.com/pololu/a4990-motor-shield
*/

/*
   Logic Table from the Driver Board
   Observered - matches table in data sheet.
     IN1/3  IN2/4  OUT1/3  OUT2/4
     (DIR)  (PWM)
     ----------------------------------
      0       0       0       1  CCLOCK (FILL)
      0       1       0       0  BRAKE
      1       0       1       1  BRAKE
      1       1       1       0  CLOCK (VENT)

   PCB DESIGN
   ----------
   Valve 0:
   IN3: Pin 8 (DIR) --> OUT3
   IN4: Pin 9 (PWM) --> OUT4

   Valve 1:
   IN1: Pin 7 (DIR) --> OUT1
   IN2: Pin 6 (PWM) --> OUT2

   Valve 2:
   IN3: Pin 4 (DIR) --> OUT3
   IN4: Pin 5 (PWM) --> OUT4

   Valve 3:
   IN1: Pin 2 (DIR) --> OUT1
   IN2: Pin 3 (PWM) --> OUT2


  D3 and D6 can be changed with TCB register (Section 21 of Atmega4809 datasheet)
  D5 and D9 should also be able to be changed, but it will affect millis() and maybe delay().
*/

#include "A4990ValveInterface.h"
const unsigned char A4990ValveInterface::_V0DIR = 8;
const unsigned char A4990ValveInterface::_V1DIR = 7;
const unsigned char A4990ValveInterface::_V2DIR = 4;
const unsigned char A4990ValveInterface::_V3DIR = 2;

const unsigned char A4990ValveInterface::_V0PWM = 9;
const unsigned char A4990ValveInterface::_V1PWM = 6;
const unsigned char A4990ValveInterface::_V2PWM = 5;
const unsigned char A4990ValveInterface::_V3PWM = 3;

// const unsigned char A4990ValveInterface::_FAULT = 6;/

bool A4990ValveInterface::_flipV0 = false;
bool A4990ValveInterface::_flipV1 = false;
bool A4990ValveInterface::_flipV2 = false;
bool A4990ValveInterface::_flipV3 = false;

A4990ValveInterface::A4990ValveInterface()
{

  // digitalWrite is called before and after setting pinMode.
  // It called before pinMode to handle the case where the board
  // is using an ATmega AVR to avoid ever driving the pin high,
  // even for a short time.
  // It is called after pinMode to handle the case where the board
  // is based on the Atmel SAM3X8E ARM Cortex-M3 CPU, like the Arduino
  // Due. This is necessary because when pinMode is called for the Due
  // it sets the output to high (or 3.3V) regardless of previous
  // digitalWrite calls.

  digitalWrite(_V0PWM, LOW);
  digitalWrite(_V1PWM, LOW);
  digitalWrite(_V2PWM, LOW);
  digitalWrite(_V3PWM, LOW);
  pinMode(_V0PWM, OUTPUT);
  pinMode(_V1PWM, OUTPUT);
  pinMode(_V2PWM, OUTPUT);
  pinMode(_V3PWM, OUTPUT);
  digitalWrite(_V0PWM, LOW);
  digitalWrite(_V1PWM, LOW);
  digitalWrite(_V2PWM, LOW);
  digitalWrite(_V3PWM, LOW);

  digitalWrite(_V0DIR, LOW);
  digitalWrite(_V1DIR, LOW);
  digitalWrite(_V2DIR, LOW);
  digitalWrite(_V3DIR, LOW);
  pinMode(_V0DIR, OUTPUT);
  pinMode(_V1DIR, OUTPUT);
  pinMode(_V2DIR, OUTPUT);
  pinMode(_V3DIR, OUTPUT);
  digitalWrite(_V0DIR, LOW);
  digitalWrite(_V1DIR, LOW);
  digitalWrite(_V2DIR, LOW);
  digitalWrite(_V3DIR, LOW);
}

// speed should be a number between -400 and 400
void A4990ValveInterface::setValve0Speed(short speed)
{
  if (speed <= 0)
  { // vent

    // saturate at -400
    if (speed < -400)
    {
      speed = -400;
    }

    digitalWrite(_V0DIR, HIGH);
    analogWrite(_V0PWM, -speed * 51 / 80);
  }
  else if (speed > 0)
  {
    // fill

    // saturate
    if (speed > 400)
      speed = 400;
    digitalWrite(_V0DIR, LOW);
    analogWrite(_V0PWM, 255 - (speed * 51 / 80));
  }
}

// speed should be a number between -400 and 400
void A4990ValveInterface::setValve1Speed(short speed)
{
  if (speed <= 0)
  { // vent

    // saturate at -400
    if (speed < -400)
    {
      speed = -400;
    }

    digitalWrite(_V1DIR, HIGH);
    analogWrite(_V1PWM, -speed * 51 / 80);
  }
  else if (speed > 0)
  {
    // fill

    // saturate
    if (speed > 400)
      speed = 400;
    digitalWrite(_V1DIR, LOW);
    analogWrite(_V1PWM, 255 - (speed * 51 / 80));
  }
}

// speed should be a number between -400 and 400
void A4990ValveInterface::setValve2Speed(short speed)
{
  if (speed <= 0)
  { // vent

    // saturate at -400
    if (speed < -400)
    {
      speed = -400;
    }

    digitalWrite(_V2DIR, HIGH);
    analogWrite(_V2PWM, -speed * 51 / 80);
  }
  else if (speed > 0)
  {
    // fill

    // saturate
    if (speed > 400)
      speed = 400;
    digitalWrite(_V2DIR, LOW);
    analogWrite(_V2PWM, 255 - (speed * 51 / 80));
  }
}

// speed should be a number between -400 and 400
void A4990ValveInterface::setValve3Speed(short speed)
{
  if (speed <= 0)
  { // vent

    // saturate at -400
    if (speed < -400)
    {
      speed = -400;
    }

    digitalWrite(_V3DIR, HIGH);
    analogWrite(_V3PWM, -speed * 51 / 80);
  }
  else if (speed > 0)
  {
    // fill

    // saturate
    if (speed > 400)
      speed = 400;
    digitalWrite(_V3DIR, LOW);
    analogWrite(_V3PWM, 255 - (speed * 51 / 80));
  }
}

// set speed for all valves
// speed should be a number between -400 and 400
void A4990ValveInterface::setSpeeds(short valve_cmd[4])
{
  setValve0Speed(valve_cmd[0]);
  setValve1Speed(valve_cmd[1]);
  setValve2Speed(valve_cmd[2]);
  setValve3Speed(valve_cmd[3]);
}

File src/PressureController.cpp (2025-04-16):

#include <stdio.h>
#include <errno.h>
#include <string.h>
#include <sstream>
#include <chrono>
#include "PressureController.hpp"
#include <unistd.h>
#include <thread>

#include <wiringPi.h>
#include <wiringSerial.h>

PressureController::PressureController(int input_num_joints)
  : Node("pressure_controller")
{
  num_joints = input_num_joints;
  this->rs485_addresses["joint_0"] = 0xFFFF;
  if (num_joints > 1) {
    this->rs485_addresses["joint_1"] = 0xFFFE;
  }
  if (num_joints > 2) {
    this->rs485_addresses["joint_2"] = 0xFFFD;
  }

  this->initialize_serial();
  this->initialize_data_vectors();
  this->ping_devices();

  // Getting the parameter rs485_config
  // rs485_addresses = this->convert_parameter_map(this->get_parameter("rs485_config"));

  // ######### Commented out by Curtis. Why do we need multithreaded operations launched here? ########
  // Add this node to the executor
  //executor.add_node(this->get_node_base_interface());

  // Start the executor in a separate thread
  //std::thread executor_thread([this, node]() {
  //    RCLCPP_INFO(this->get_logger(), "Starting executor");
  //    executor.spin();  // Spin the executor to process callbacks
  //});
  //executor_thread.detach();  // Detach the thread to run asynchronously

  this->start_subscribers();
  this->start_publishers();

  control_thread = std::thread([this]() {this->serial_loop();});
  control_thread.detach();
}

PressureController::~PressureController()
{
  serialFlush(this->fd);
  serialClose(this->fd);
}

// Pings each of the serial devices and throws errors if any are not responding correctly
void PressureController::ping_devices()
{
  serialFlush(this->fd);
  RCLCPP_INFO(this->get_logger(), "Checking communication with serial devices...");

  for (int joint = 0; joint < num_joints; joint++)
  {
    unsigned short joint_address = this->rs485_addresses["joint_" + std::to_string(joint)];
    RCLCPP_INFO(this->get_logger(), "Pinging joint %d", joint_address);

    prepare_outgoing_bytes(joint);

    write(this->fd, this->outgoing_bytes, BYTES_IN_PACKET);

    bool timeout = wait_for_response(2000);

    if (!timeout)
    {
      if (handle_incoming_bytes(joint))
      {
        RCLCPP_INFO_STREAM(this->get_logger(), "Joint " << joint_address << " ping successful.");
      }
      else
      {
        RCLCPP_WARN(this->get_logger(), "Unsucessful read");
        //RCLCPP_ERROR_ONCE(this->get_logger(), "Not all devices found. Killing node.");
        //rclcpp::shutdown();
	throw std::runtime_error("Communication attempted and failed. Killing node.");
      }
    }
    else
    {
      RCLCPP_ERROR_ONCE(this->get_logger(), "Not all devices found. Killing node.");
      //rclcpp::shutdown();
      throw std::runtime_error("Timeout. Killing node.");
    }
  }
}

// Continously loops the inputting and outputting of the serial data
void PressureController::serial_loop()
{
  rclcpp::Duration max_loop_time(0, 0);
  unsigned long num_loops = 0;
  unsigned long num_corrupted = 0;
  unsigned long num_timeout = 0;

  while (rclcpp::ok())
  {
    rclcpp::Time loop_start = this->get_clock()->now(); 
    RCLCPP_INFO_STREAM_ONCE(this->get_logger(), "PRESSURE CONTROL STARTED");

    for (int joint = 0; joint < num_joints; joint++)
    {
      if (DEBUG_MODE)
      {
        // rclcpp::Duration(.03, 0).sleep();
      }

      serialFlush(fd); // clear the current serial buffer before doing anything with it, RX AND TX

      prepare_outgoing_bytes(joint);

      if (DEBUG_MODE)
      {
        printf("Pressure commands: ");
	this->mutex_lock.lock();
        for (int i = 0; i < 4; i++)
        {
          printf("%f ", this->pressure_commands[joint][i]);
        }
        printf("\n");
	this->mutex_lock.unlock();

        printf("Address + outgoing pressure command shorts: ");
        for (int i = 0; i < 5; i++)
        {
          printf("%d ", this->outgoing_shorts[i]);
        }
        printf("\n");

        printf("Address + outgoing pressure command bytes: ");
        for (int i = 0; i < 10; i++)
        {
          printf("%02x ", this->outgoing_bytes[i]);
        }
        printf("\n");
      }

      if (write(this->fd, this->outgoing_bytes, BYTES_IN_PACKET) != 10)
      {
        RCLCPP_WARN(this->get_logger(), "Incorrect amount of bytes sent.");
      }

      bool timeout = wait_for_response(2);

      if (!timeout)
      {
        if (handle_incoming_bytes(joint))
        {
          // convert analog shorts to kpa and load for sending over ROS
	  this->mutex_lock.lock();
          for (int i = 0; i < num_pressures_per_joint; i++)
          {
            float tmp = analog_to_kpa(this->incoming_data_shorts[i]);
            this->pressures[joint][i] = filter(this->pressures[joint][i], tmp);
          }
	  this->mutex_lock.unlock();

          if (DEBUG_MODE)
          {
            printf("Converted to pressures: ");
	    this->mutex_lock.lock();
            for (int i = 0; i < 4; i++)
            {
              printf("%f ", this->pressures[joint][i]);
            }
            printf("\n");
	    this->mutex_lock.unlock();
          }

          // reset counters since communication was succesful
          joint_missed_counter[joint] = 0;
        }
        else
        {
          // printf("Unsucessful read. Data not saved.\n");
          num_corrupted++;
          joint_missed_counter[joint]++;
        }
      }
      else
      {
        num_timeout++;
        joint_missed_counter[joint]++;

        // empty both RX and TX buffers
        serialFlush(fd);
      }

      //check if we have lots of consecutive misses, likely something broke
      if (joint_missed_counter[joint] > 50)
      {
        RCLCPP_ERROR(this->get_logger(), "Lost connection with joint %d", joint);
      }
    }

    rclcpp::Duration loop_time = this->get_clock()->now() - loop_start;
    if (loop_time > max_loop_time)
    {
      max_loop_time = loop_time;
    }

    num_loops++;

    if (DEBUG_MODE)
    {
      RCLCPP_INFO_STREAM(this->get_logger(), "Loop Time: " << this->get_clock()->now().seconds() - loop_start.seconds() << " s");
      std::cout << std::endl;
    }
  }

  // print serial communication statistics
  std::cout << "\n\nSERIAL COMMUNICATION STATISTICS\n" << std::endl;
  std::cout << "Max Loop Time: " << max_loop_time.seconds() << " s" << std::endl;
  std::cout << "Corrupted " << float(num_corrupted) / num_loops * 100 << "% of messages" << std::endl;
  std::cout << "Timed out " << float(num_timeout) / num_loops * 100 << "% of messages\n\n" << std::endl;
}
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

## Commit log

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2020-04-22 Changes to be committed: new file: I2CDevice.cpp new file: I2CDevice.h
2020-04-22 Added setting ip on startup and launching imu and pressure control on boot Changes to be committed: modified: bb_install_script.sh new file: set_ip_on_startup
2020-04-22 I think this install script works, but only for pressure control, not IMU publishing too
2020-04-23 Things build, but haven't tested on hardware yet. Changes to be committed: modified: src/I2CDevice.h modified: src/PressureController.cpp modified: src/PressureController.h modified: src/i2c_pressure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
2020-04-23 i2c_pressure_control.cpp works to detect multiple i2c devices and make different publishers and subscribers for each. Changes to be committed: modified: CMakeLists.txt modified: src/I2CDevice.cpp mod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
2020-04-24 Pressure controller accepts multiple nodes based on how many are there when starting. I have verified that the Arduino is receiving pressure commands I have verified that the BBB is getting pressures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
2020-05-13 This arduino code ran the real grub and it worked well.
2020-05-26 Committing the Arduino code after changing the move_valve function to take in a positive or negative number
2020-06-09 Made the IMUPublisher like the PressureController in structure and format Changes to be committed: modified: CMakeLists.txt new file: src/IMUPublisher.cpp new file: src/IMUPublisher.h modified: src/i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
2020-06-09 IMU pose estimation works reasonably well. Need to calibrate IMUs and try Changes to be committed: modified: arduino_code/arduino_imu_pose_estimation/arduino_imu_pose_estimation.ino modified: arduino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
2020-06-09 Commit from beaglebone. IMUPublisher works well. Changes to be committed: modified: src/IMUPublisher.cpp modified: src/i2c_imu_publisher.cpp
2020-06-10 Made calibration script for IMUs and IMU pose estimation works well.
2020-06-10 Added visualization for arduino IMU pose estimation Changes to be committed: new file: Visualizer.pde
2020-06-18 Changes to be committed: deleted: arduino_imu_pose_estimation/Visualizer.pde modified: arduino_imu_pose_estimation/arduino_imu_pose_estimation.ino
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2020-06-30 Phil's final commit of imu pose estimation from work computer. modified: ../arduino_code/arduino_imu_pose_estimation/arduino_imu_pose_estimation.ino
2020-06-30 Changes to be committed: modified: CMakeLists.txt deleted: arduino_code/arduino_imu_calibration/arduino_imu_calibration.ino deleted: arduino_code/arduino_imu_pose_estimation/arduino_imu_pose_estimati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
2020-06-30 Added PCB files to pcb_design folder
    [Sch_v3.brd, Sch_v3.sch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]
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2020-11-22 Created folder for older versions of the PCB
    [Sch_v3.brd]
2020-11-22 pcb_design/Sch_v3.sch edited online with Bitbucket
    [Sch_v3.sch]
2020-11-23 Updated PCB files
    [Sch_v4.brd, Sch_v4.sch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]
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2021-01-25 updated to v5. Cleaned up schematic a bit. Still need to fix I2C, flipped pins, etc.
    [Sch_v4.brd, Sch_v4.sch, Sch_v5.brd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]
2021-01-26 Fixed I2C traces, changed power on arduino from VCC pin to Raw, updated silkscreen
    [Sch_v5.brd, Sch_v5.sch]
2021-01-30 adding M3 mounting holes with no solder mask
    [Sch_v5.brd, Sch_v5.sch]
2021-02-09 added byu parts library
    [Sch_v5.brd, Sch_v5.sch]
2021-02-16 commiting recent work
    [Sch_v5.brd, Sch_v5.sch]
2021-02-16 board routed
    [Sch_v5.brd]
2021-02-16 added BBB cape beginning
    [BBB_cape.brd, BBB_cape.sch]
2021-02-16 final version of pcb I think
    [Sch_v5.brd, Sch_v5.sch]
2021-02-17 added dip switch. autorouting completed
    [Sch_v5.brd, Sch_v5.sch]
2021-02-17 fixed small bug
    [Sch_v5.brd]
2021-02-17 fixed another bug
    [Sch_v5.brd]
2021-02-18 adding library and design rules
    [Sch_v4.GBL, Sch_v4.GBS, Sch_v4.GTL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]
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2021-02-24 last few changes and CAM outputs generated
    [Sch_v5.brd, Sch_v5.csv, Sch_v5.sch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]
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2021-03-12 all 4 pressures are being sent across ROS sucessfully
2021-03-17 pushing from beaglebone. new pcb working, callback not working - Curtis
    [PressureController.cpp]
2021-05-07 added v6 with better connectors and some small drill changes
    [BBB_cape.brd, BBB_cape.sch, Sch_v6.brd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]
2021-05-10 removed old files and updated with CAM files for both pcbs.
    [BBB_cape.brd, BBB_cape.sch, Sch_v3.brd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]
2021-05-17 added checking for expected i2c_devices
    [leg_hardware.yaml]
2021-05-29 fixed spacing in bbb cape
    [BBB_cape.brd]
2021-06-01 updated files and cams
    [BBB_cape.brd, BBB_cape.sch, Sch_v6.brd]
2021-06-01 added pics of new pcb
    [pressure_control_v6.brd, pressure_control_v6.sch]
2021-06-04 added arduino test script and cleaned up stuff in control script.
2021-06-14 fixed rosparam not loading bug
    [leg_hardware.yaml]
2021-06-14 fixed topic numbering bug
    [PressureController.cpp]
2021-06-15 added valve library interface for much cleaner code.
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2021-06-25 fixed dependency on radmsg
    [PressureController.cpp]
2021-07-20 added ability to switch between 8bit and 16 bit precision. Also upgraded to ROS noetic.
2021-07-20 added ability on arduino to switch between 8bit and 16bit precision
2022-05-26 changed Pressure command subscribers to 1 queue size with tcpnodelay.
2022-06-17 added command line arg for numjoints to easily switch between configurations
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2023-07-31 Adding odroid + arduino code for sending RS485 serial comms
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2023-08-16 arduino_code.ino edited online with Bitbucket. Working call response. Needs to be integrated into i2c code and cleaned up
2023-08-23 Removed i2c related code, adjusted PressureController.cpp with code from RS485_code and updated arduino_pressure_control
2023-09-01 fixing addresses on arduino
    [main.cpp]
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2023-09-11 addding packetized reset after responding to avoid buffer overflow
    [main.cpp]
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2023-09-19 tuned PID, as agressive as possible without jittering
    [main.cpp]
2023-09-20 fix accidental push cleanup
    [PressureController.cpp]
2023-09-20 remove old stuff
    [BBB_cape.brd, BBB_cape.sch, pressure_control_v6.brd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]
2023-10-06 added raising errors instead of just print statements
    [PressureControllerPython.cpp]
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2024-02-27 added software LPF with fast fixed point math
    [main.cpp]
2024-02-27 updated to long type to avoid overflow bug in LPF.
    [main.cpp]
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2024-05-07 detuned a bit for smoother performance. Still little SS error.
    [main.cpp]
2024-05-08 fixed bug where arduino continuously tries to vent before pneudrive is running. Caused excessive heat up on hardware
    [main.cpp]
2024-05-17 fixed big jump on startup bug
    [main.cpp]
2024-05-20 adding some error checking on arduino side.
    [main.cpp]
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2025-04-16 Unified case in the code, fit CMakeLists.txt and package.xml to ROS 2 standard, and added clarifications in the READMEs
